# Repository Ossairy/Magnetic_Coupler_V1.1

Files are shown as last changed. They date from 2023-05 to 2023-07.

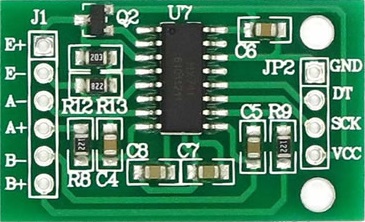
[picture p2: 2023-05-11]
PCB Design/vertion 4/3d/hx711.jpeg

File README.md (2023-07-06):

# Magnetic_Coupler

Project Objective :  
   
    the project objective is to design and manufacture Motor testing setup.
    
Project Duration :
    
    August 2021 ; during my internship period in MRS research Lab -Multi Robot Systems- in german university in cairo.
    
Project Description :   
    First the system is designed and modeled on Solidworks and then the designed parts is manufactured using Laser cutting machine , conventional Lathe , conventional milling machine ,and CNC bending machine. It was desired to measure the torque of a motor that wanted to be tested however applying so much force on the motor shaft may hurt the motor ,so I choosed the magnetic coupler to be added to the system to add the following :
        - Mechanical fusing.
        - No load starting.
At the end the system succeded to acheive the desired objective to measure the motor torque , no load speed electrical power ,and efficiency.

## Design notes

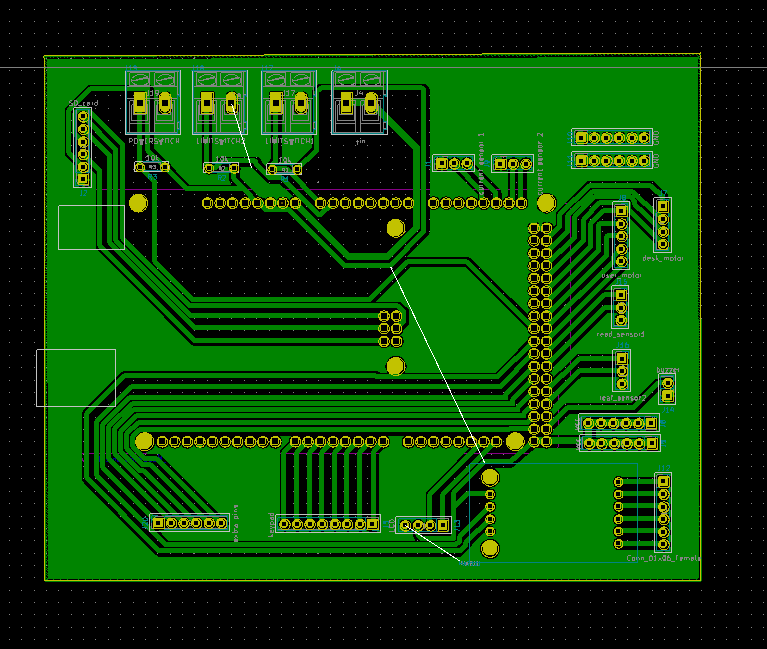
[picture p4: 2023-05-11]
PCB Design/vertion 4/pcb.PNG

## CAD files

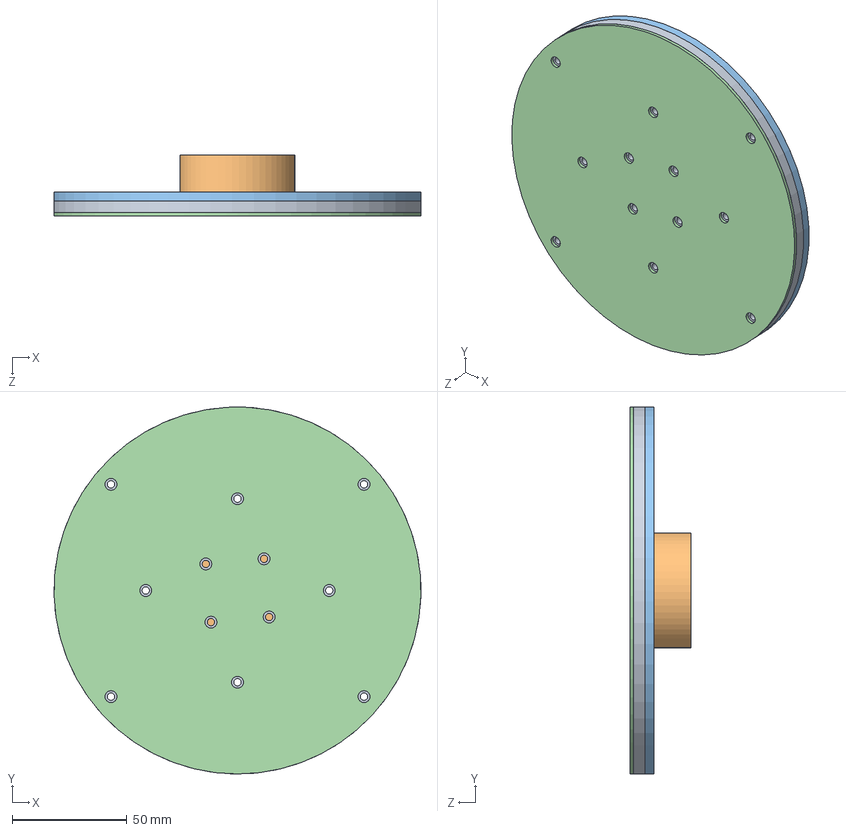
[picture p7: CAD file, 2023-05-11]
3D_Modeling/Magnitic gear assem/Magnitic gear Assem.SLDASM
160.0 x 160.0 x 26.5 mm
Magnitic Disk
Disk holder
Magnet Back limit
magnetic gear cover
Magnet x 18

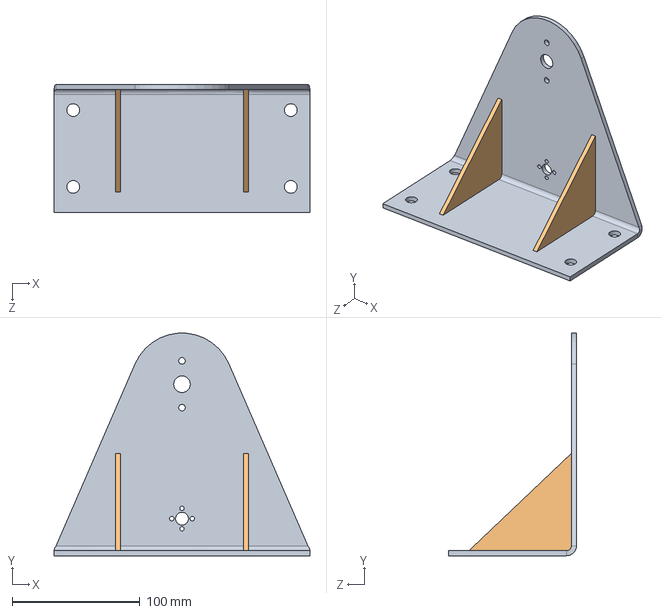
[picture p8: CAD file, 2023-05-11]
3D_Modeling/Sheet Metal/Driven Holder Assem.SLDASM
200.0 x 173.8 x 100.0 mm
Sheet Metal driven holder
Driven holder rip x 2

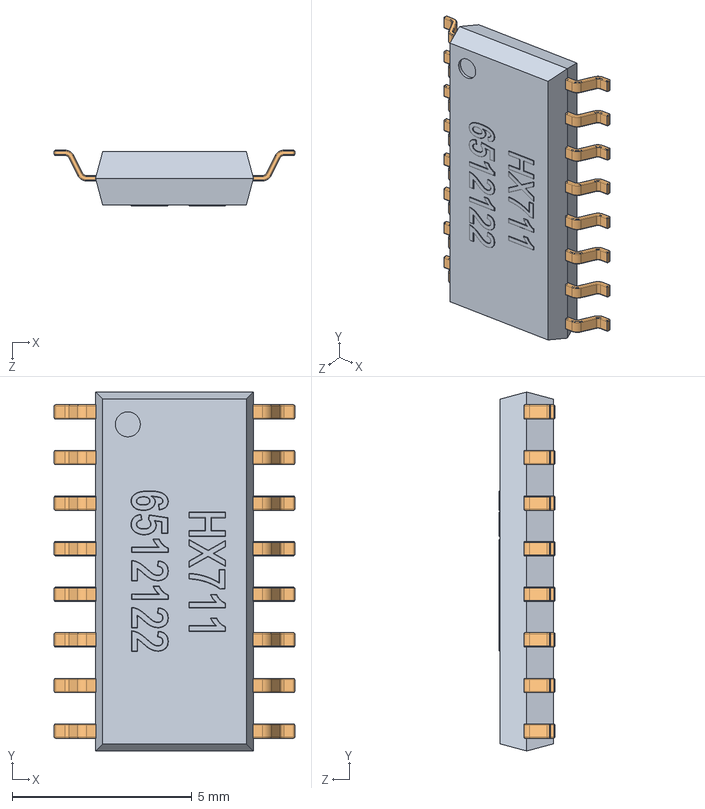
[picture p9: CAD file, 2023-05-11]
PCB Design/vertion 4/3d/HX711_SOP16.SLDASM
6.70 x 10.0 x 1.56 mm
base_HX711
pino_HX711 x 16

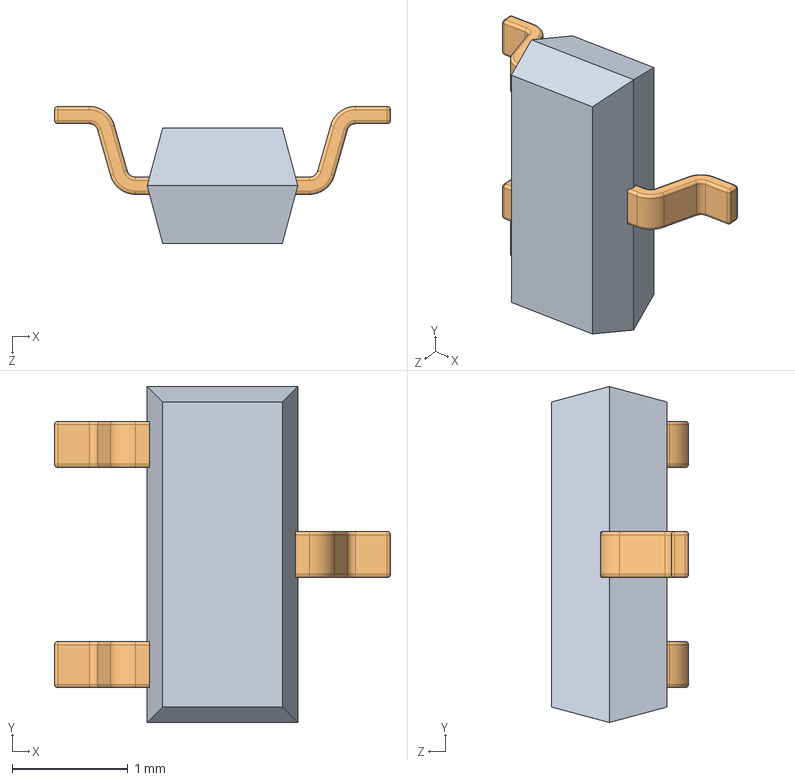
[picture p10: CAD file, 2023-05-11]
PCB Design/vertion 4/3d/SOT23.SLDASM
2.90 x 2.90 x 1.19 mm
TRANSISTOR_SOT23
PINO_SOT23 x 3

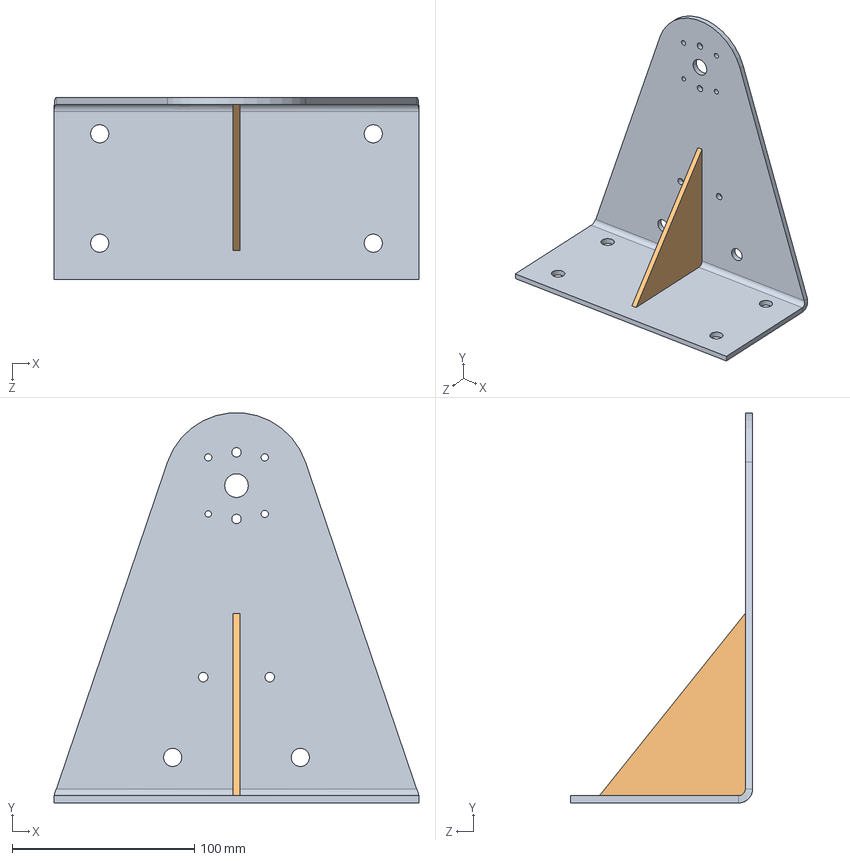
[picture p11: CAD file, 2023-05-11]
3D_Modeling/Sheet Metal/Driver Holder Assem.SLDASM
200.0 x 213.8 x 100.0 mm
Sheet Metal driver holder
Driver holder rib

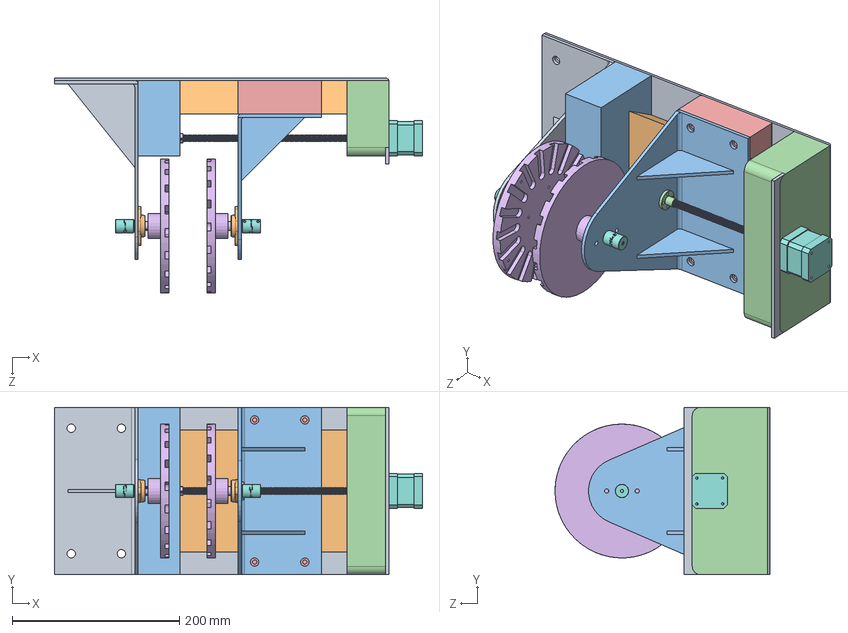
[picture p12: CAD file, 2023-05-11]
3D_Modeling/Assem1.SLDASM
440.0 x 200.0 x 257.0 mm
chassis
lower linear traveller
screw supporter
Motor holder
Upper linear traveller x 2
608RS x 3
MOSCAM2,5 x 2
Nema 17
driver holder
KFL08 x 2
driven holder
8mm Lead Screw
screw bar
magnitic gear x 2
bar x 2
coupling_5x8 x 2

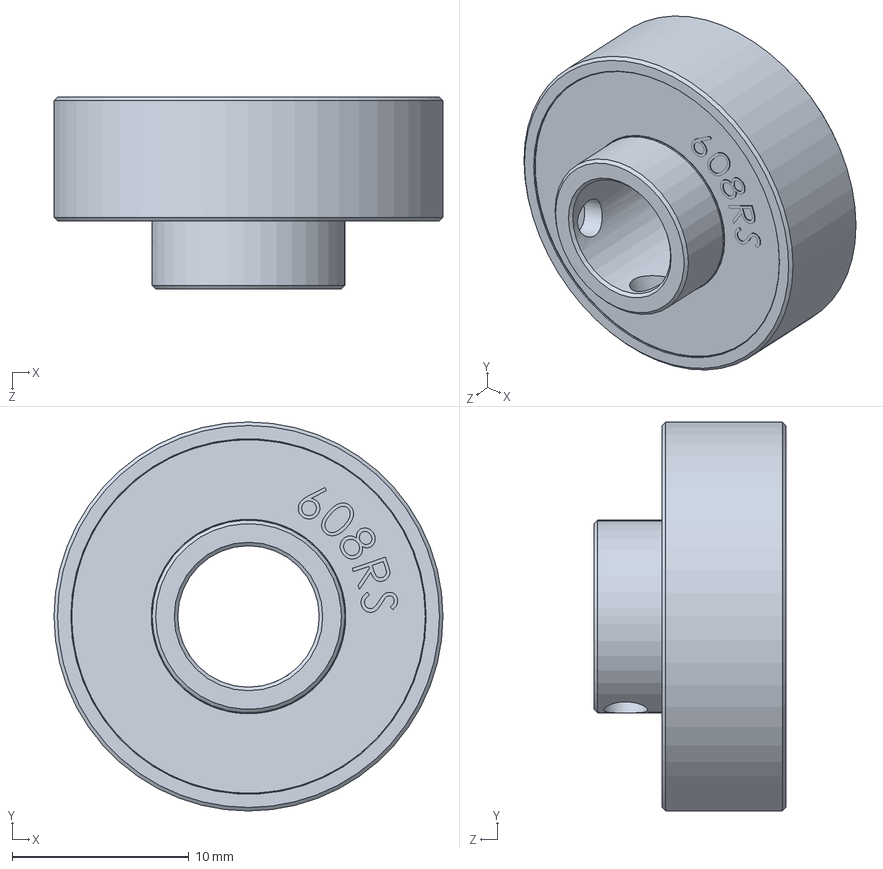
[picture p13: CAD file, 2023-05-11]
3D_Modeling/608RS.SLDPRT
22.0 x 22.0 x 10.9 mm

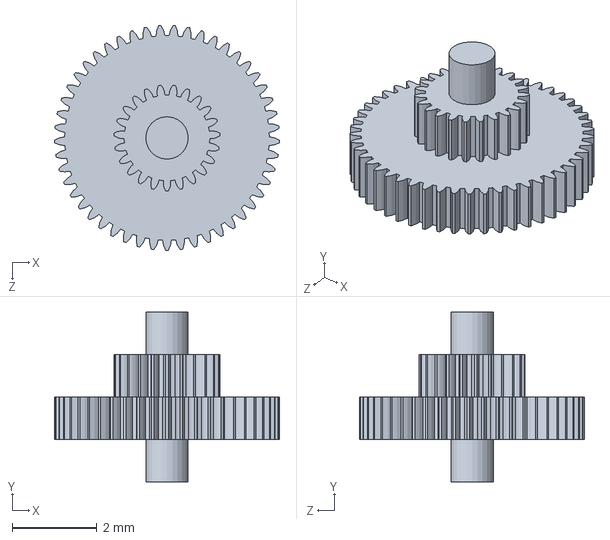
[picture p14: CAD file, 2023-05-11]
3D_Modeling/Motor 12V/Motor JGB37-545/Part 4.SLDPRT
5.30 x 4.00 x 5.30 mm

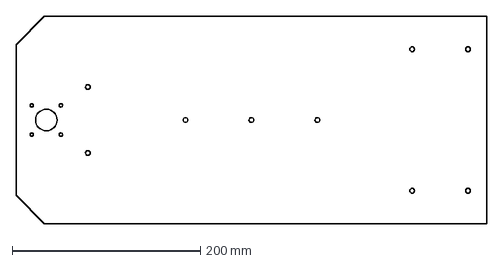
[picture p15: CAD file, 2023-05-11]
3D_Modeling/Sheet Metal/dxf files/Flat pattern - Sheet Metal chassis.DXF
499.8 x 220.0 mm

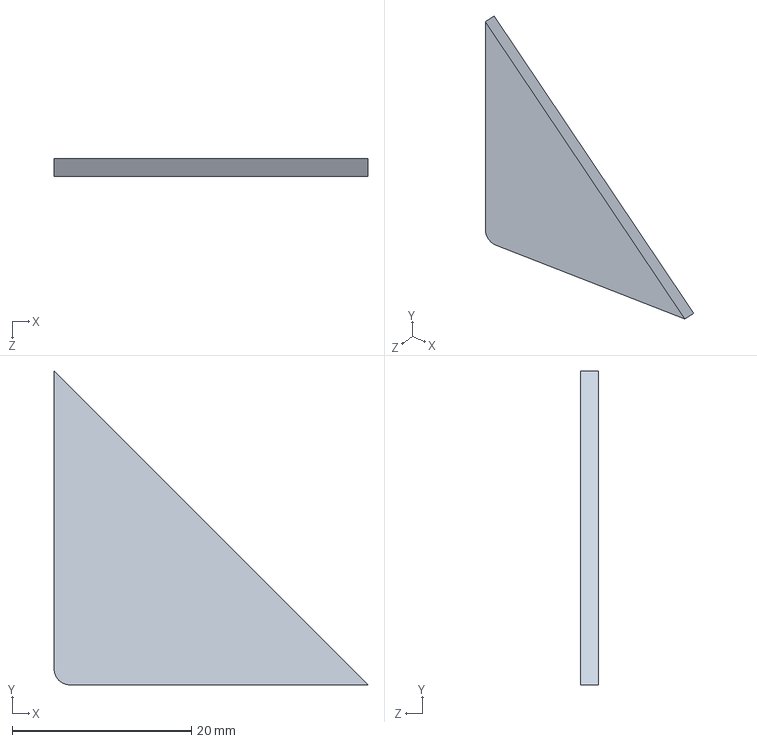
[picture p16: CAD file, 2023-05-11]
3D_Modeling/Sheet Metal/Nema17 rib.SLDPRT
35.0 x 35.0 x 2.00 mm

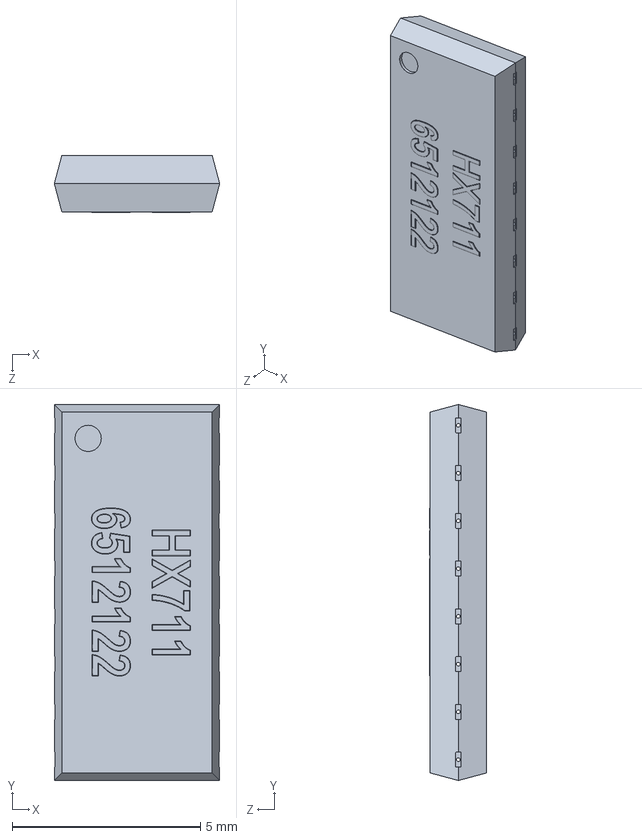
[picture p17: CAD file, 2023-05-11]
PCB Design/vertion 4/3d/base_HX711.SLDPRT
4.40 x 10.0 x 1.52 mm

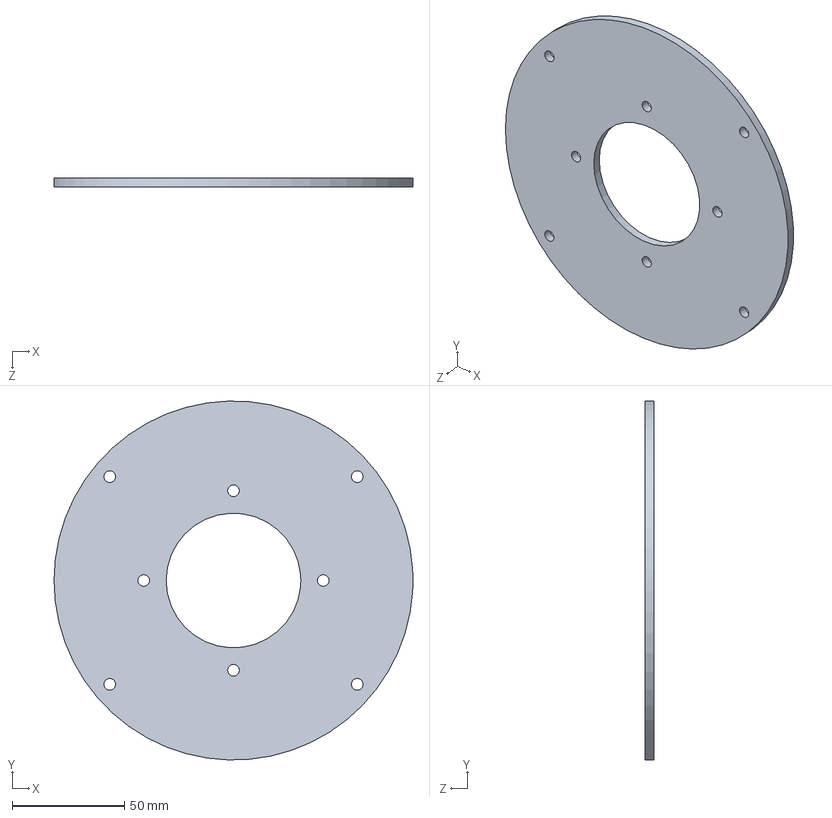
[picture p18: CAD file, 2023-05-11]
3D_Modeling/Magnitic gear assem/Magnet Back limit.SLDPRT
160.0 x 159.9 x 4.00 mm

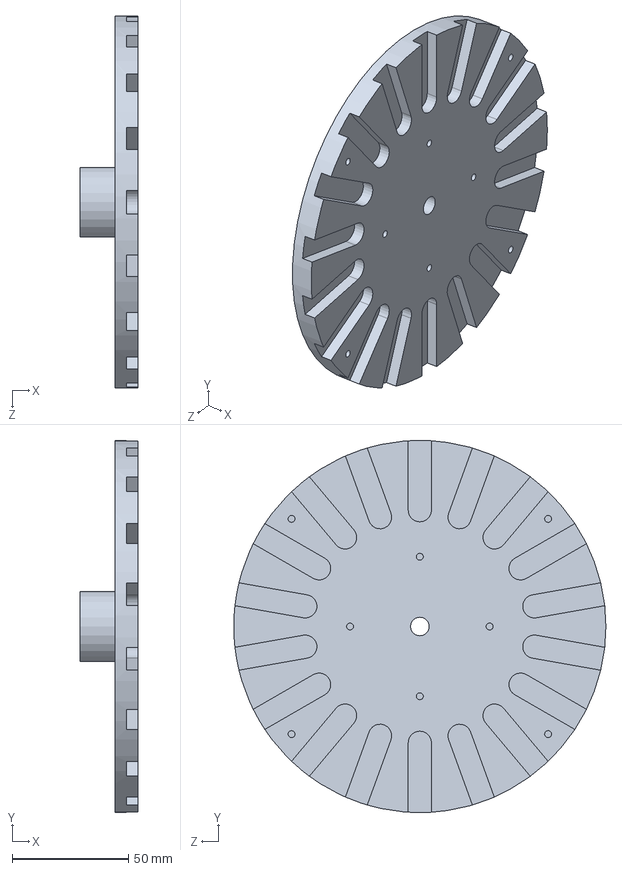
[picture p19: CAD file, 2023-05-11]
3D_Modeling/magnitic gear.SLDPRT
25.0 x 159.9 x 159.9 mm

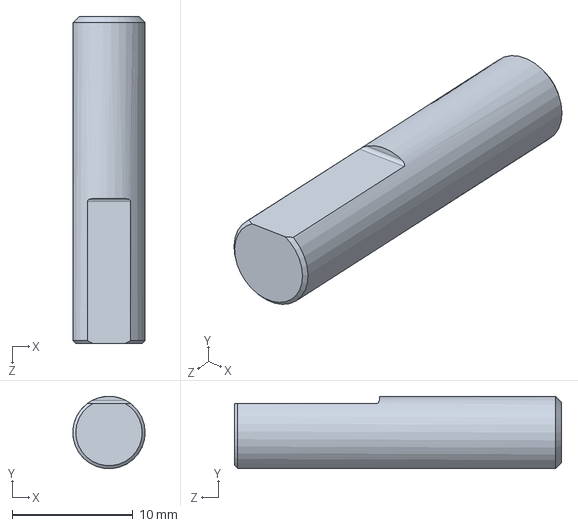
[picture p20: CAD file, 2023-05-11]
3D_Modeling/Motor 12V/Motor JGB37-545/Shaft.SLDPRT
6.00 x 5.99 x 27.1 mm

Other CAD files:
3D_Modeling/Sheet Metal/dxf files/Flat pattern - Sheet Metal Nema17 LBracket.DXF
PCB Design/vertion 4/3d/ArduinoMega.SLDPRT
3D_Modeling/Magnitic gear assem/Disk holder.SLDPRT
3D_Modeling/Motor 12V/Motor JGB37-545/Motor body.SLDPRT
3D_Modeling/Drawing/Modified magnitic gear drawing.SLDDRW
3D_Modeling/Drawing/Nema17 LBracket drawing.SLDDRW
3D_Modeling/Drawing/Upper linear traveller drawing.SLDDRW
3D_Modeling/Drawing/chassis Drawing.SLDDRW
3D_Modeling/Drawing/driven holder drawing.SLDDRW
3D_Modeling/Drawing/driver holder drawing.SLDDRW
3D_Modeling/Drawing/lower linear traveller drawing.SLDDRW
3D_Modeling/Drawing/magnitic gear drawing.SLDDRW
3D_Modeling/KFL08.SLDPRT
3D_Modeling/Lead Screw.SLDPRT
3D_Modeling/Load_cell_sensor-5_kg v1.step.SLDPRT
3D_Modeling/M3 Bolt.SLDPRT
3D_Modeling/M3 nut.SLDPRT
3D_Modeling/M5 bolt.SLDPRT
3D_Modeling/M5 nut.SLDPRT
3D_Modeling/Magnet.SLDPRT
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

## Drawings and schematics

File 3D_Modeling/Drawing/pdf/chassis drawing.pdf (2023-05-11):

6

5

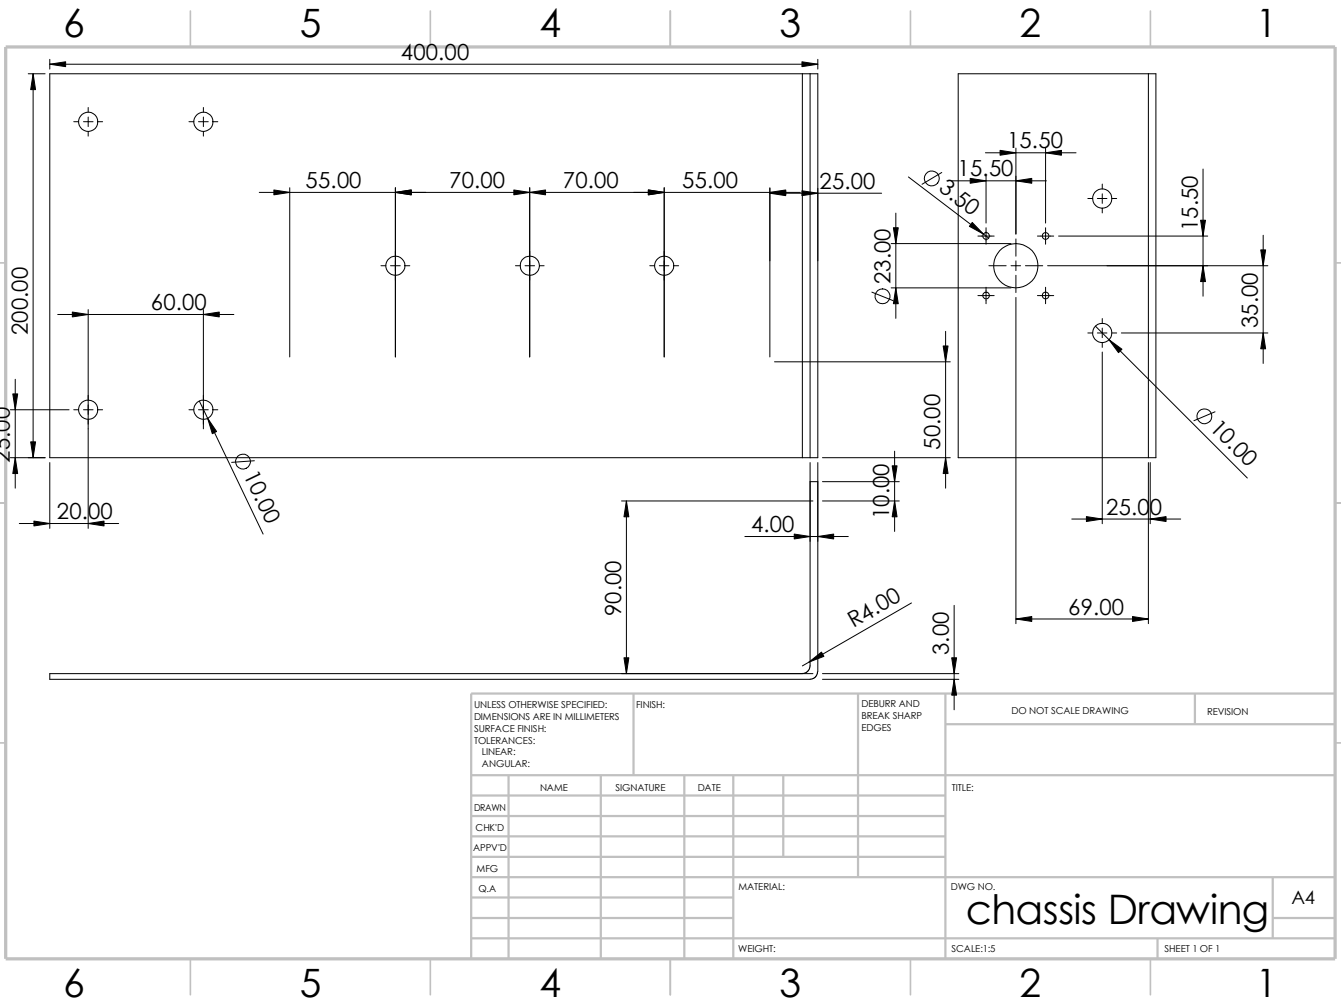
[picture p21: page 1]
WEIGHT:; SCALE:1:5; SHEET 1 OF 1; REVISION; FINISH:; EDGES; DEBURR AND BREAK SHARP; chassis Drawing ²³.00

DO NOT SCALE DRAWING UNLESS OTHERWISE SPECIFIED:
DIMENSIONS ARE IN MILLIMETERS
SURFACE FINISH:
TOLERANCES:
LINEAR:
ANGULAR:

NAME | SIGNATURE | DATE | | | | TITLE:

DRAWN
CHK'D
APPV'D
Q.A | | | | MATERIAL: | DWG NO. | A4

MFG

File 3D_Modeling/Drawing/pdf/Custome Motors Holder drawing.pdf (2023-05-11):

6

5

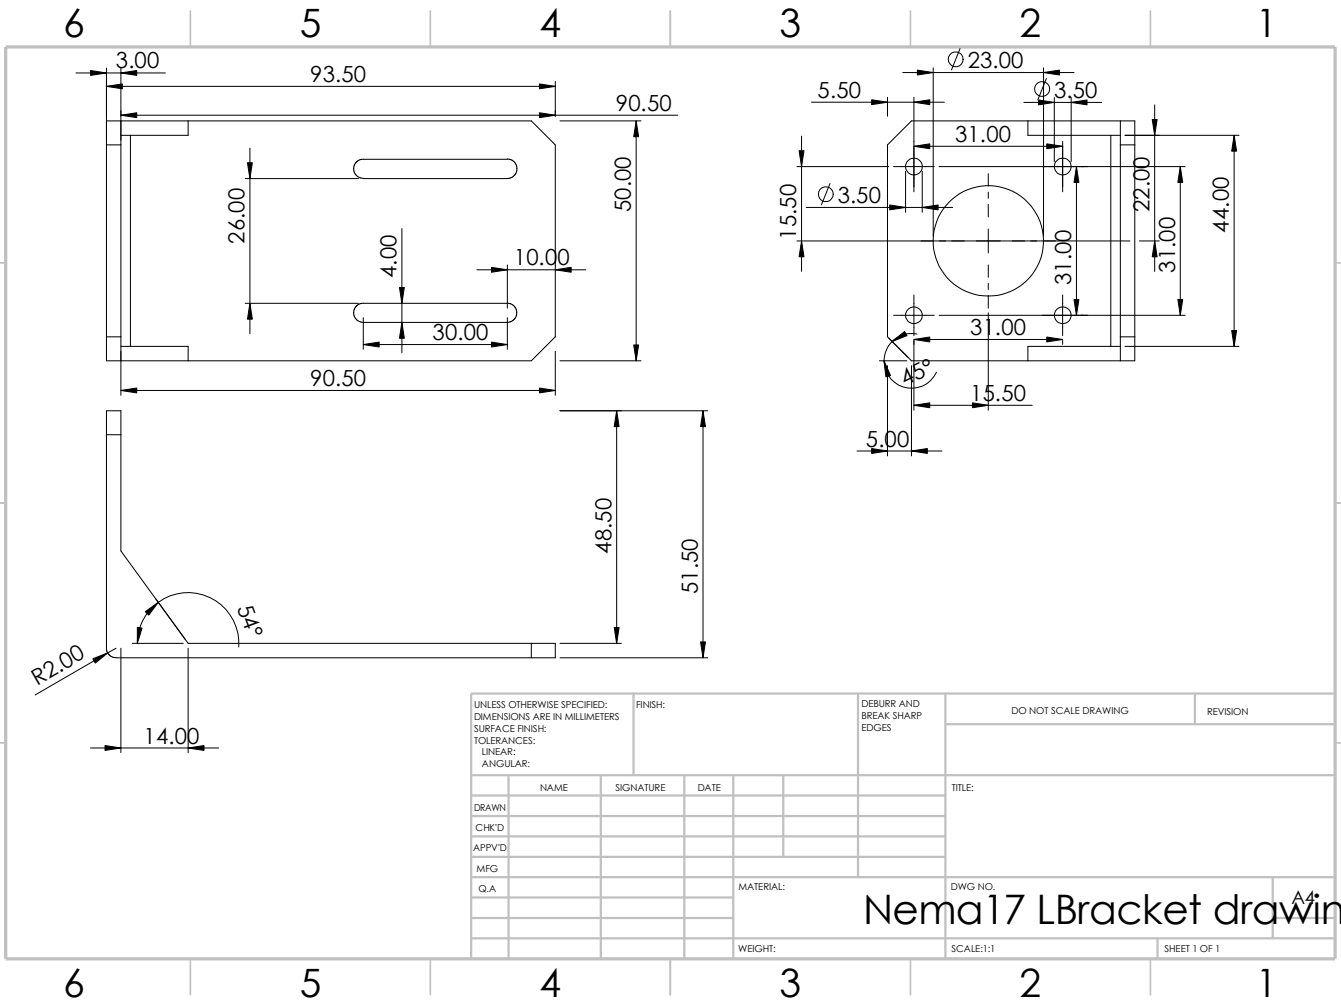
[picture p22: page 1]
WEIGHT:; SCALE:1:1; SHEET 1 OF 1; REVISION; FINISH:; EDGES; DEBURR AND BREAK SHARP; Nema17 LBracket drawing ⁴⁸.50

DO NOT SCALE DRAWING UNLESS OTHERWISE SPECIFIED:
DIMENSIONS ARE IN MILLIMETERS
SURFACE FINISH:
TOLERANCES:
LINEAR:
ANGULAR:

NAME | SIGNATURE | DATE | | | | TITLE:

DRAWN
CHK'D
APPV'D
Q.A | | | | MATERIAL: | DWG NO. | A4

MFG

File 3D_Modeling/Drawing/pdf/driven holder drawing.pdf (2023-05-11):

6

5

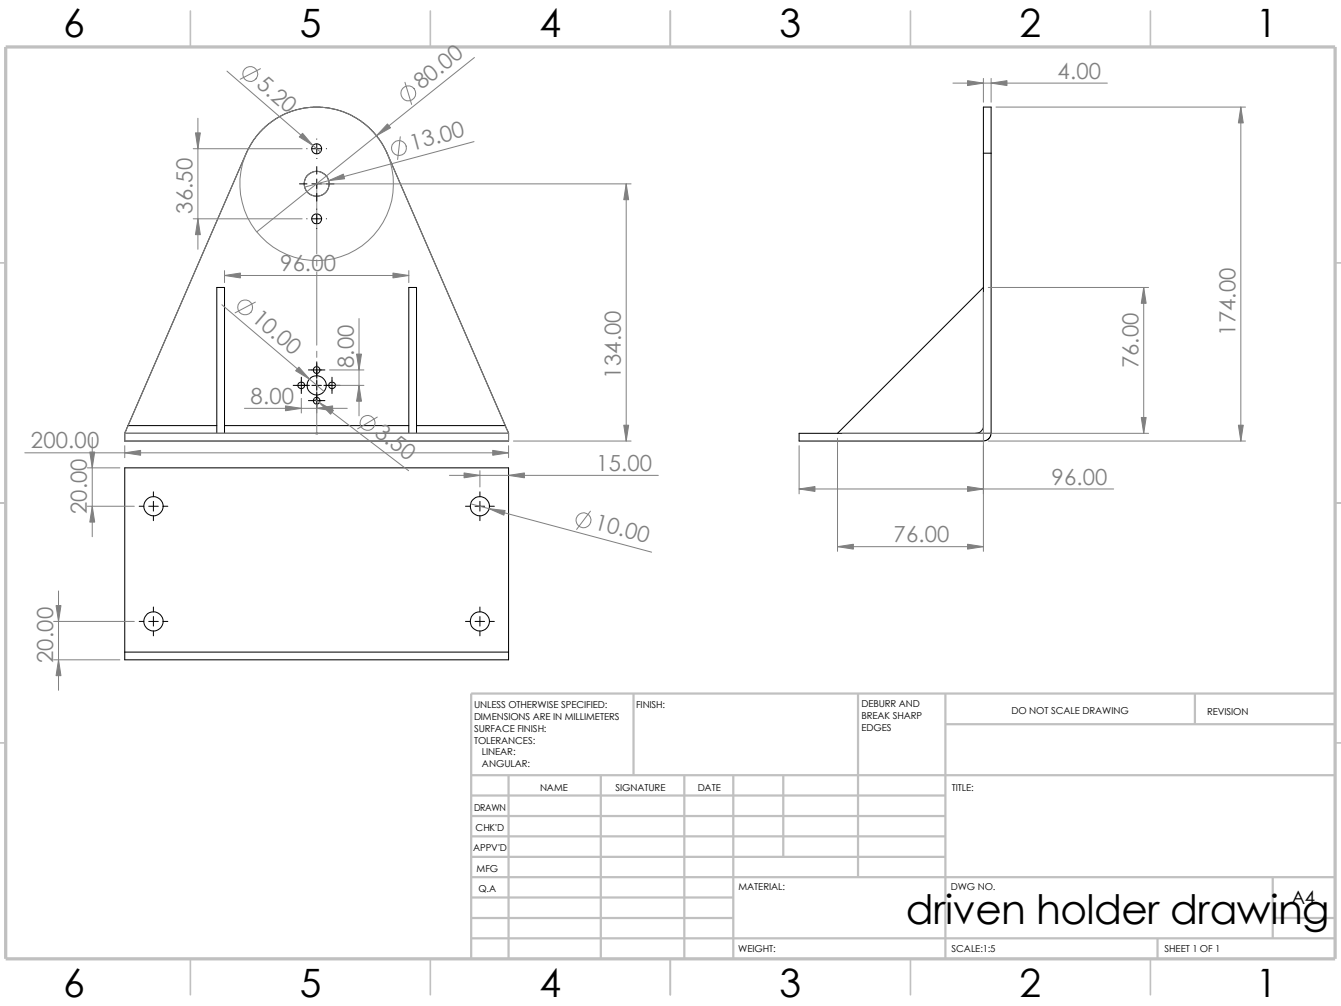
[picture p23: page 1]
WEIGHT:; SCALE:1:5; SHEET 1 OF 1; REVISION; FINISH:; EDGES; DEBURR AND BREAK SHARP

DO NOT SCALE DRAWING UNLESS OTHERWISE SPECIFIED:
DIMENSIONS ARE IN MILLIMETERS
SURFACE FINISH:
TOLERANCES:
LINEAR:
ANGULAR:

NAME | SIGNATURE | DATE | | | | TITLE:

DRAWN
CHK'D
APPV'D
Q.A | | | | MATERIAL: driven holder drawing | DWG NO. | A4

MFG

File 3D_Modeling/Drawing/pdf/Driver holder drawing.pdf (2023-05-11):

6

5

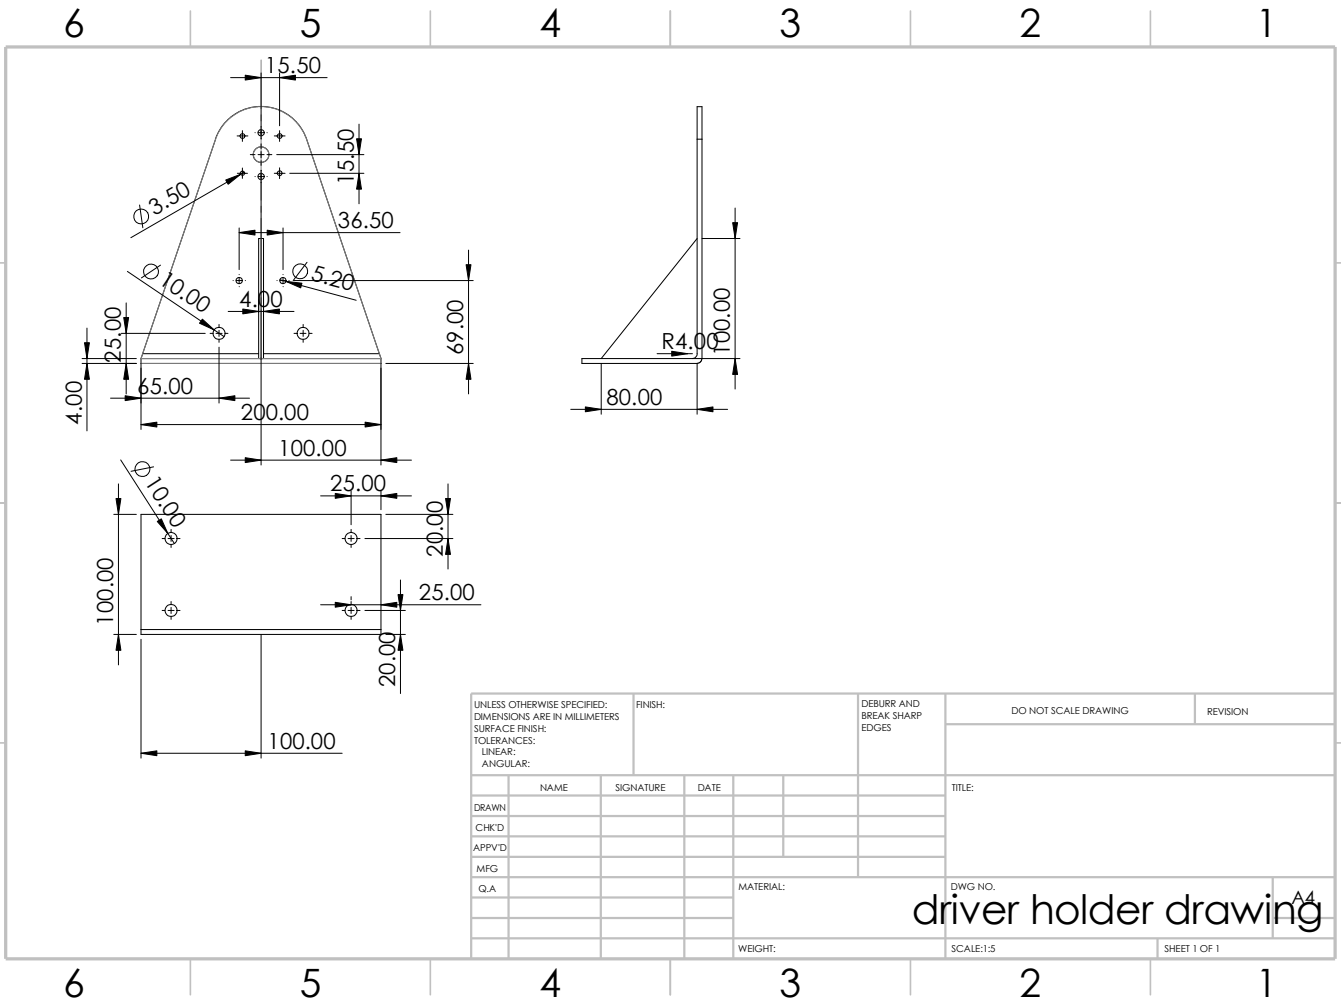
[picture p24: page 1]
WEIGHT:; SCALE:1:5; SHEET 1 OF 1; REVISION; FINISH:; EDGES; DEBURR AND BREAK SHARP; 100.00 ¹⁰⁰.00

DO NOT SCALE DRAWING UNLESS OTHERWISE SPECIFIED:
DIMENSIONS ARE IN MILLIMETERS
SURFACE FINISH:
TOLERANCES:
LINEAR:
ANGULAR:

NAME | SIGNATURE | DATE | | | | TITLE:

DRAWN
CHK'D
APPV'D
Q.A | | | | MATERIAL: driver holder drawing | DWG NO. | A4

MFG

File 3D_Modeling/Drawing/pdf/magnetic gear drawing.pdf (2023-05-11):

6

5

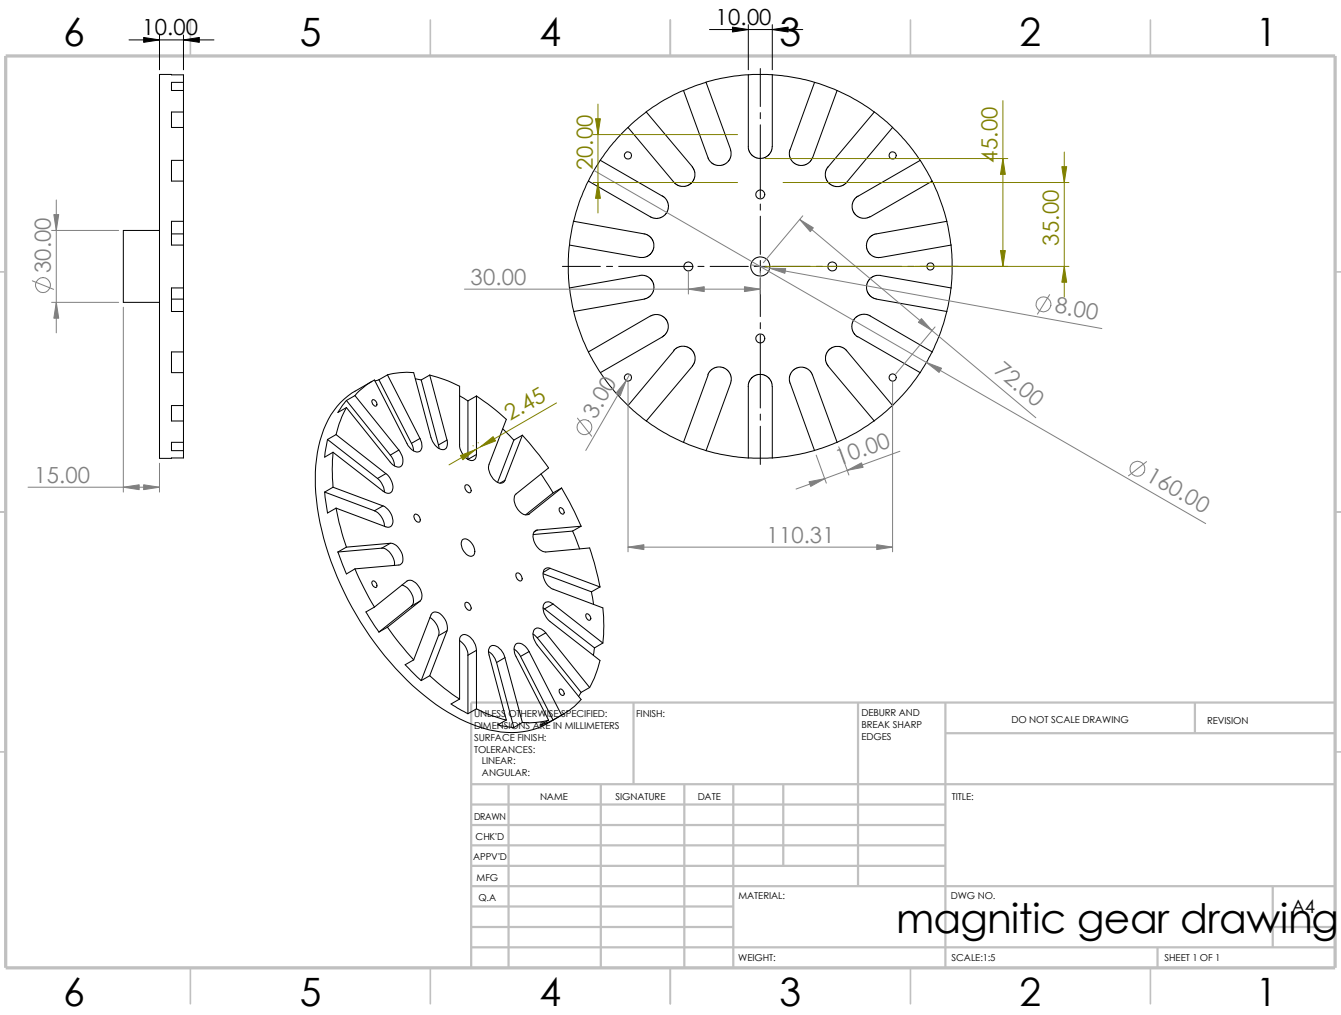
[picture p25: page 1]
WEIGHT:; SCALE:1:5; SHEET 1 OF 1; FINISH:; EDGES; DO NOT SCALE DRAWING; REVISION; DEBURR AND BREAK SHARP

UNLESS OTHERWISE SPECIFIED:
DIMENSIONS ARE IN MILLIMETERS
SURFACE FINISH:
TOLERANCES:
LINEAR:
ANGULAR:

NAME | SIGNATURE | DATE | | | | TITLE:

DRAWN
CHK'D
APPV'D

MFG
Q.A | | | | MATERIAL: magnitic gear drawing | DWG NO. | A4

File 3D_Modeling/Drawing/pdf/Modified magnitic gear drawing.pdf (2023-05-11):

6

5

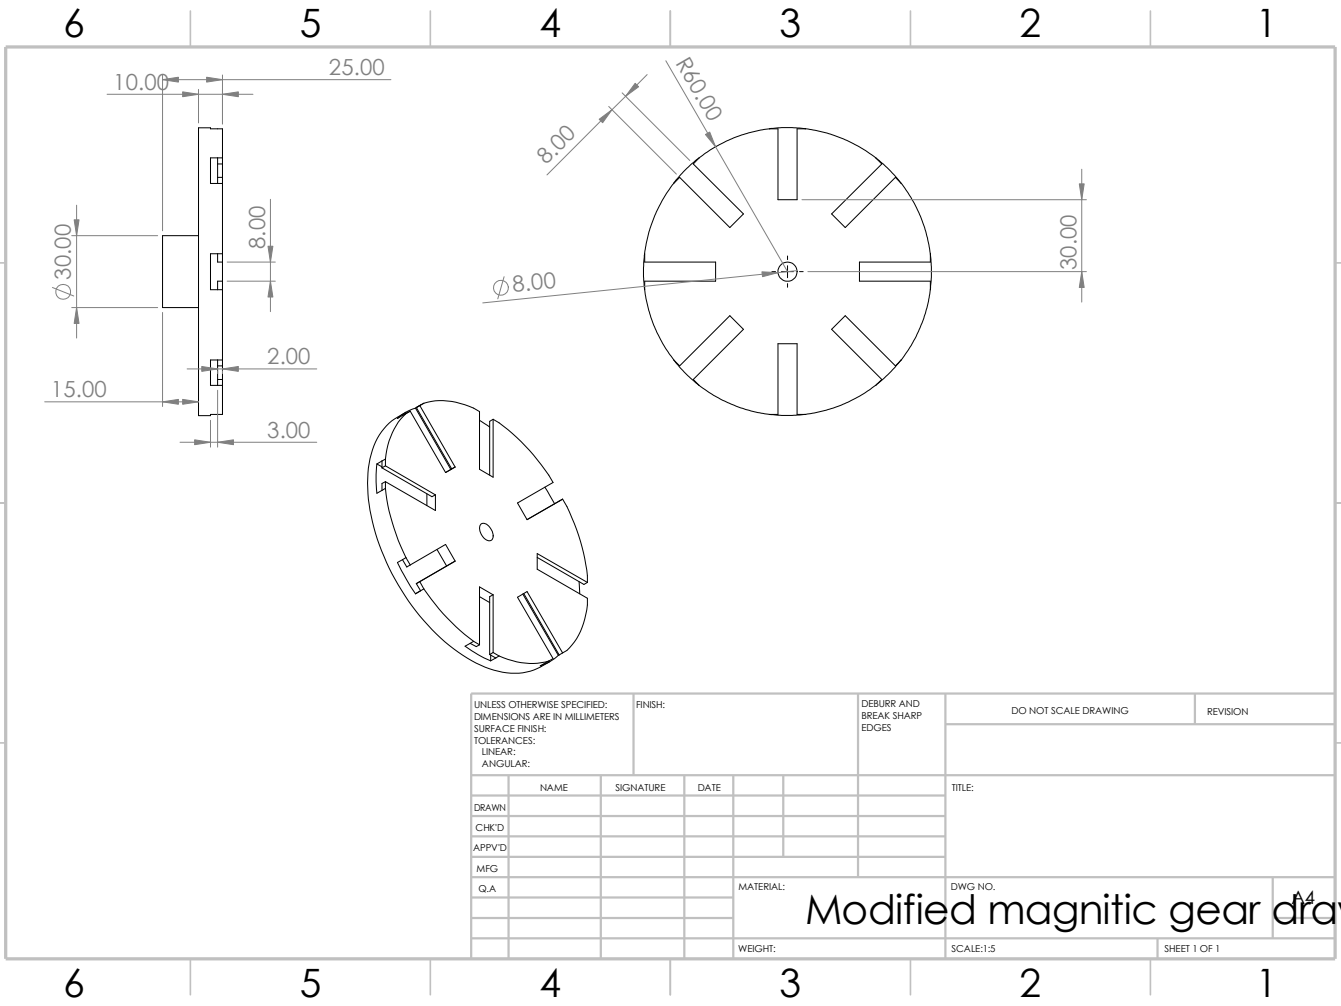
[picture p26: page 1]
WEIGHT:; SHEET 1 OF 1; SCALE:1:5; FINISH:; EDGES; DO NOT SCALE DRAWING; REVISION; DEBURR AND BREAK SHARP

UNLESS OTHERWISE SPECIFIED:
DIMENSIONS ARE IN MILLIMETERS
SURFACE FINISH:
TOLERANCES:
LINEAR:
ANGULAR:

NAME | SIGNATURE | DATE | | | | TITLE:

DRAWN
CHK'D
APPV'D

MFG
Q.A | | | | MATERIAL: | DWG NO. | A4

Modified magnitic gear drawing

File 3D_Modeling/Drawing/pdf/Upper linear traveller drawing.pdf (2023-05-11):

6

5

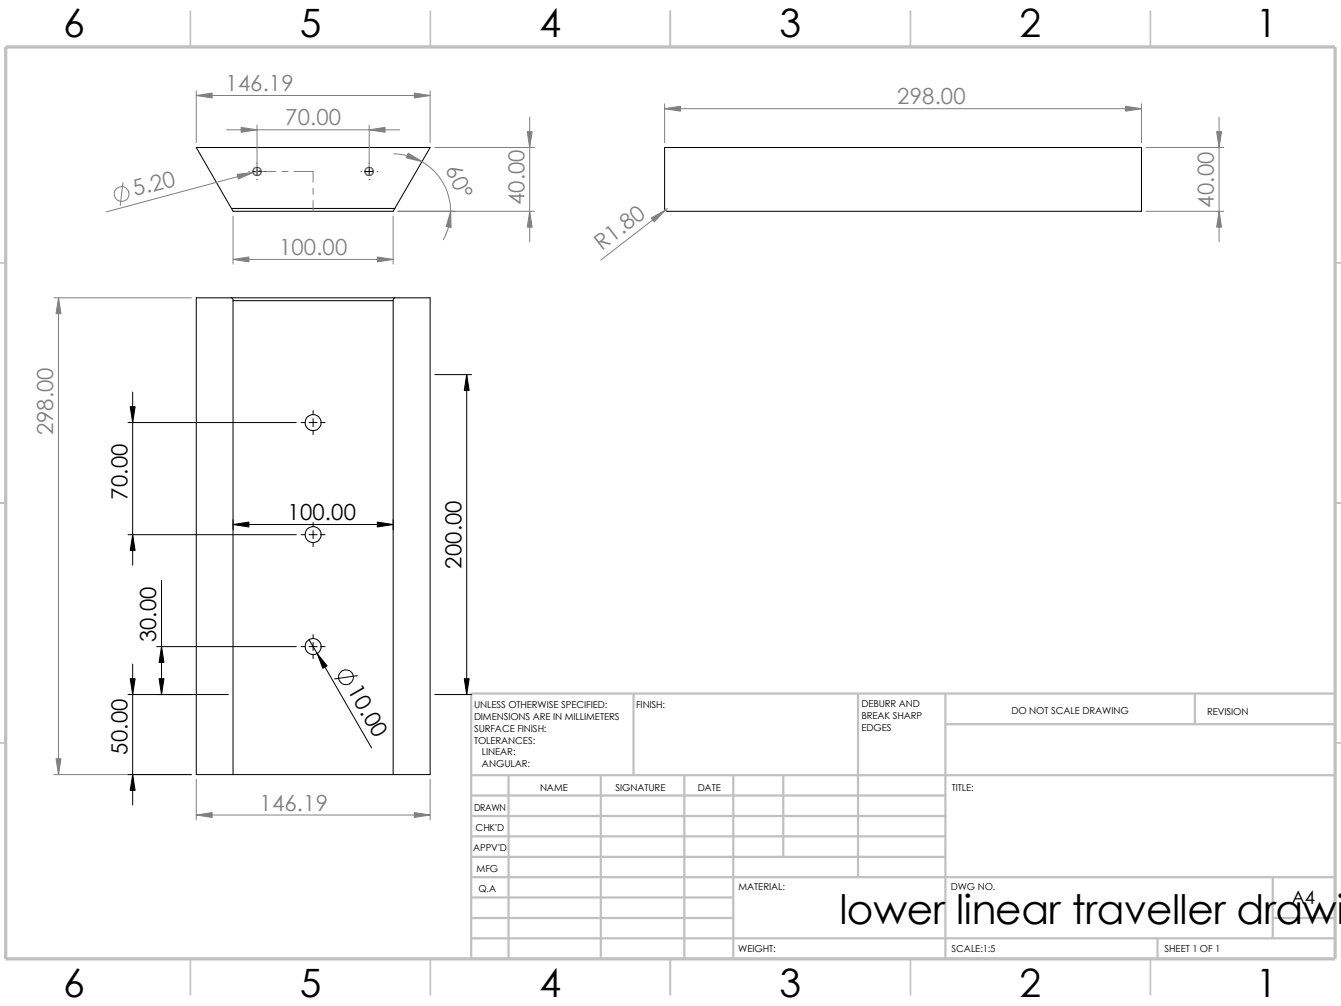
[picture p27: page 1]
WEIGHT:; SCALE:1:5; SHEET 1 OF 1; FINISH:; EDGES; DO NOT SCALE DRAWING; REVISION; DEBURR AND BREAK SHARP; 146.19 ²⁹⁸.00

UNLESS OTHERWISE SPECIFIED:
DIMENSIONS ARE IN MILLIMETERS
SURFACE FINISH:
TOLERANCES:
LINEAR:
ANGULAR:

NAME | SIGNATURE | DATE | | | | TITLE:

DRAWN
CHK'D
APPV'D

MFG
Q.A | | | | MATERIAL: | DWG NO. | A4

lower linear traveller drawing

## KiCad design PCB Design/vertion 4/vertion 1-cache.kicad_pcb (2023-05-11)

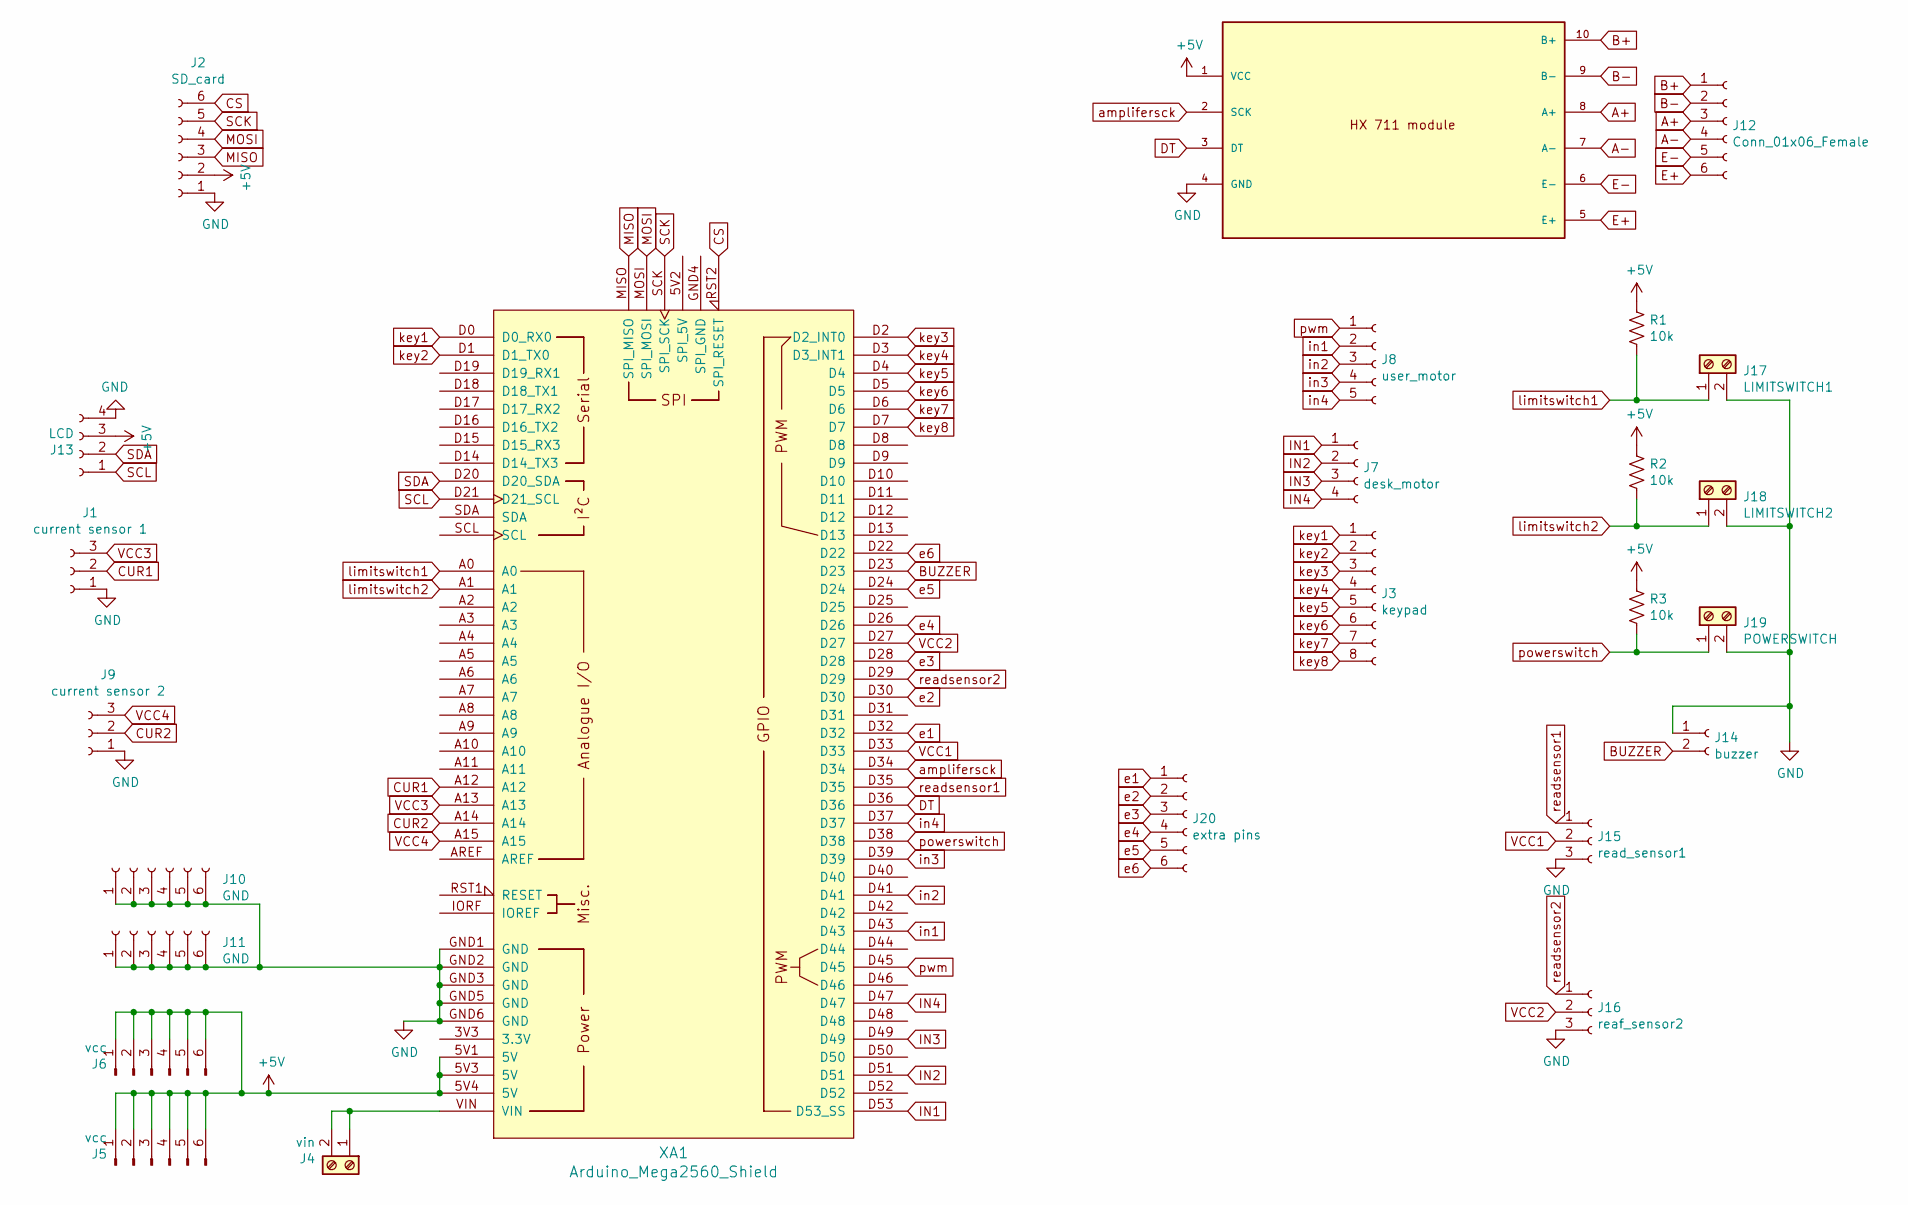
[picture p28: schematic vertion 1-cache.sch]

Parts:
HX7111: HX711
J1: current sensor 1; PinSocket_1x03_P2.54mm_Vertical
J2: SD_card; PinSocket_1x06_P2.54mm_Vertical
J3: keypad; PinSocket_1x08_P2.54mm_Vertical
J4: vin; TerminalBlock_Altech_AK300-2_P5.00mm
J5, J6: vcc; PinHeader_1x06_P2.54mm_Vertical
J7: desk_motor; PinSocket_1x04_P2.54mm_Vertical
J8: user_motor; PinSocket_1x05_P2.54mm_Vertical
J9: current sensor 2; PinSocket_1x03_P2.54mm_Vertical
J10, J11: GND; PinHeader_1x06_P2.54mm_Vertical
J12: Conn_01x06_Female; PinSocket_1x06_P2.54mm_Vertical
J13: LCD; PinSocket_1x04_P2.54mm_Vertical
J14: buzzer; PinSocket_1x02_P2.54mm_Vertical
J15: read_sensor1; PinSocket_1x03_P2.54mm_Vertical
J16: reaf_sensor2; PinSocket_1x03_P2.54mm_Vertical
J17: LIMITSWITCH1; TerminalBlock_Altech_AK300-2_P5.00mm
J18: LIMITSWITCH2; TerminalBlock_Altech_AK300-2_P5.00mm
J19: POWERSWITCH; TerminalBlock_Altech_AK300-2_P5.00mm
J20: extra pins; PinSocket_1x06_P2.54mm_Vertical
R1, R2, R3: 10k; R_Axial_DIN0204_L3.6mm_D1.6mm_P5.08mm_Horizontal
XA1: Arduino_Mega2560_Shield

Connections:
+5V: HX7111.1 (VCC), J2.2, J5.1, J5.2, J5.3, J5.4, J5.5, J5.6, J6.1, J6.2, J6.3, J6.4, J6.5, J6.6, J13.3, R1.1, R2.1, R3.1, XA1.5V1 (5V), XA1.5V3 (5V), XA1.5V4 (5V)
A+: HX7111.8 (A+), J12.3
A-: HX7111.7 (A-), J12.4
B+: HX7111.10 (B+), J12.1
B-: HX7111.9 (B-), J12.2
BUZZER: J14.2, XA1.D23
CS: J2.6, XA1.RST2 (SPI_RESET)
CUR1: J1.2, XA1.A12
CUR2: J9.2, XA1.A14
DT: HX7111.3 (DT), XA1.D36
E+: HX7111.5 (E+), J12.6
E-: HX7111.6 (E-), J12.5
GND: HX7111.4 (GND), J1.1, J2.1, J9.1, J10.1, J10.2, J10.3, J10.4, J10.5, J10.6, J11.1, J11.2, J11.3, J11.4, J11.5, J11.6, J13.4, J14.1, J15.3, J16.3, J17.2, J18.2, J19.2, XA1.GND1 (GND), XA1.GND2 (GND), XA1.GND3 (GND), XA1.GND5 (GND), XA1.GND6 (GND)
IN1: J7.1, XA1.D53 (D53_SS)
IN2: J7.2, XA1.D51
IN3: J7.3, XA1.D49
IN4: J7.4, XA1.D47
MISO: J2.3, XA1.MISO (SPI_MISO)
MOSI: J2.4, XA1.MOSI (SPI_MOSI)
unnamed: J4.1, J4.2, XA1.VIN
SCK: J2.5, XA1.SCK (SPI_SCK)
SCL: J13.1, XA1.D21 (D21_SCL)
SDA: J13.2, XA1.D20 (D20_SDA)
VCC1: J15.2, XA1.D33
VCC2: J16.2, XA1.D27
VCC3: J1.3, XA1.A13
VCC4: J9.3, XA1.A15
amplifersck: HX7111.2 (SCK), XA1.D34
e1: J20.1, XA1.D32
e2: J20.2, XA1.D30
e3: J20.3, XA1.D28
e4: J20.4, XA1.D26
e5: J20.5, XA1.D24
e6: J20.6, XA1.D22
in1: J8.2, XA1.D43
in2: J8.3, XA1.D41
in3: J8.4, XA1.D39
in4: J8.5, XA1.D37
key1: J3.1, XA1.D0 (D0_RX0)
key2: J3.2, XA1.D1 (D1_TX0)
key3: J3.3, XA1.D2 (D2_INT0)
key4: J3.4, XA1.D3 (D3_INT1)
key5: J3.5, XA1.D4
key6: J3.6, XA1.D5
key7: J3.7, XA1.D6
key8: J3.8, XA1.D7
limitswitch1: J17.1, R1.2, XA1.A0
limitswitch2: J18.1, R2.2, XA1.A1
powerswitch: J19.1, R3.2, XA1.D38
pwm: J8.1, XA1.D45
readsensor1: J15.1, XA1.D35
readsensor2: J16.1, XA1.D29

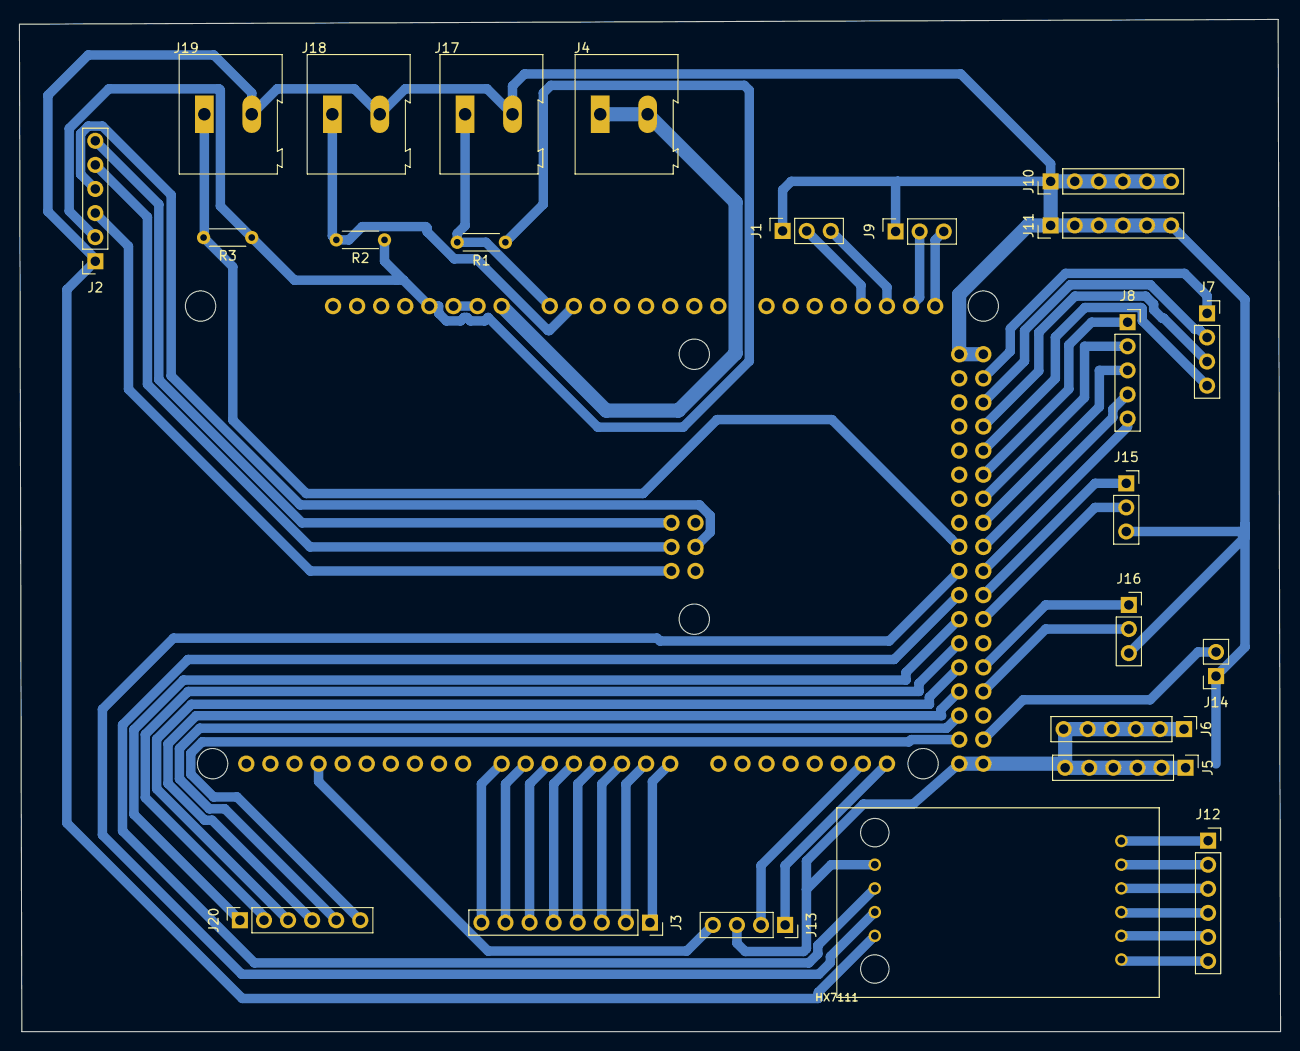
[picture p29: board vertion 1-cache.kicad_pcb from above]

Board: 2 copper layers, 133.0 x 106.8 mm, 25 parts (1 on the bottom side), 52 nets.

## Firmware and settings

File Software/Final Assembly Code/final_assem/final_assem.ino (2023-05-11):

#include <Keypad.h>
#include <Wire.h>
#include <Adafruit_GFX.h>
#include <Adafruit_SSD1306.h>

#include <Stepper.h>

#include "HX711.h"

#define calibration_factor -17090.00 //This value is obtained using the SparkFun_HX711_Calibration sketch

#define LOADCELL_DOUT_PIN  36
#define LOADCELL_SCK_PIN  34

HX711 scale;

int torque;
const int stepsPerRevolution = 200;
Stepper myStepper = Stepper(stepsPerRevolution, 53, 51, 49, 47);

float power;
float current ;

int a =  0;
float value =0;
int avgRpm ;
int count=0;

float loops;
int rpm = 0;
int b [30] ;
float maxSpeed =0;
float minSpeed=0;
float accelerasion;



//int a =  0;
//float value =0;
int a2 =  0;
float value2 =0;
//unsigned long long t =0;
//loat loops;
float loops2;
//int rpm = 0;
int rpm2 = 0;
//float maxSpeed =0;
//float accelerasion;
int maxtorque;

// Declaration for an SSD1306 display connected to I2C (SDA, SCL pins)
//Adafruit_SSD1306 display(SCREEN_WIDTH, SCREEN_HEIGHT, &Wire, -1);

const byte ROWS = 4;
const byte COLS = 4;

char hexaKeys[ROWS][COLS] = {
  {'1', '2', '3', '+'},
  {'4', '5', '6', '-'},
  {'7', '8', '9', 'x'},
  {'.', '0', '=', '/'}
};
 
// Connections to Arduino
byte rowPins[ROWS] = {7, 6, 5, 4}; //connect to the row pinouts of the keypad
byte colPins[COLS] = {3, 2, 44, 22}; //connect to the column pinouts of the keypad
 
// Create keypad object
Keypad customKeypad = Keypad(makeKeymap(hexaKeys), rowPins, colPins, ROWS, COLS);
 /*
class Motor {
  public :
   String Name ;
   int Torque ; 
   int Maxrpm ; 
   int Power ; 
   int efficiency ;
   public:
    Motor (String Name , int Torque , int Maxrpm , int Power , int efficiency ){
      this->Name = Name;
      this->Torque = Torque;
      this->Maxrpm = Maxrpm;
      this->Power = Power;
      this->efficiency = efficiency;
      
      init();
      
      }
  int measureSPEED (){
  
Serial.println(" qq measuring SPEED (rpm) ......");

}
int measurePOWER (){
  
Serial.println("  qq measuring POWER (rpm) ......");

}
int measureTORQUE (){
  
Serial.println("  qq measuring TORQUE (rpm) ......");

}
  
  };*/

//Motor Nema17 =Motor("Nema17",260,1500,30,80);
//Motor Nema23 =Motor("Nema23",600,1800,40,90);
bool Measureflag = false;
bool Motorflag =false;
bool Modeflag =false;
//Motor  recordedmotors [] = {Nema17 , Nema23};
int arrlength = 2;
void setup() {
//Serial.begin(115200);
pinMode(23,OUTPUT);

pinMode(25 , INPUT) ;

pinMode(43 , OUTPUT) ;
pinMode(45 , OUTPUT) ;
pinMode(24 , INPUT) ;
digitalWrite (13, LOW) ;
pinMode(41 , OUTPUT) ;

pinMode(53,OUTPUT);
pinMode(51,OUTPUT);
pinMode(47,OUTPUT);

pinMode(27 , OUTPUT);
digitalWrite(27,HIGH);
pinMode(33,OUTPUT);
digitalWrite(33,HIGH);
pinMode(A13,OUTPUT);
digitalWrite(A13,HIGH);
pinMode(A15,OUTPUT);
digitalWrite(A15,HIGH);
//pinMode(33,OUTPUT);


Serial.begin(9600);
 scale.begin(LOADCELL_DOUT_PIN, LOADCELL_SCK_PIN);
  scale.set_scale(calibration_factor);
  //scale.tare();
pinMode(31,INPUT);
pinMode(29,INPUT);
}

void loop() {
 
if(!Modeflag)
  getMode();

if(digitalRead(38))
 Modeflag = false;


}


void testandreport(){
Serial.println("DO YOU WANT RECORDED DATA OF STANDARD MOTORS");
Serial.println(" 1) Yes. ");
Serial.println(" 2) Compare with my data. ");
Serial.println(" 3) Back. ");
  while(1){
    char customKey = customKeypad.getKey();
    if(customKey){
       if(customKey == '1'){
        //Motor a = choosefromrecorded();
        //Motor b = a;
        // b.Maxrpm = b.measureSPEED();
         //b.Power = b.measurePOWER();
         //b.Torque = b.measureTORQUE();
         // compare method needed
         return  ;
        
       }
       else if(customKey == '2'){
        
       }
       else if (customKey == '3'){
        getMode();
       }


      
    }
  }

  
}


void choosefromrecorded(){
 /*int l =sizeof(recordedmotors);
  while(1){
 for(int i=0 ; i< arrlength ; i++ ){

  Serial.print(i+1);
  Serial.print(") ");
  Serial.println(recordedmotors[i].Name);
  
 }
  int x = getnum() -1 ;
  if ( x >arrlength){
    Serial.println("please choose a motor listed");
  }
   else 
     return ;
  
}*/
}





void getMotorParameter(){
 


 
}
  void getMode(){
  

//bool Modeflag =false;
Serial.println("PLEASE CHOOSE MODE");
Serial.println(" 1) measure .");
Serial.println(" 2) test and report . ");
//display.println("Hello, world!");
  //display.display(); 

 
 while(1){
    char customKey = customKeypad.getKey();
    if(customKey){
      
     if(customKey == '1'){
        Modeflag = true;
        measure();
        
        Serial.println(".......THANK YOU.......");

digitalWrite(23,HIGH);
delay(500);
digitalWrite(23,LOW);
delay(100);
digitalWrite(23,HIGH);
delay(500);
digitalWrite(23,LOW);
delay(100);
digitalWrite(23,HIGH);
delay(500);
digitalWrite(23,LOW);


        return;
   
  }

     else if(customKey == '2'){
       Modeflag = true;
       testandreport();


          Serial.println();
       Serial.print("The recorded speed :");
          Serial.println();
       Serial.print("The recorded torque :");
          Serial.println();
       Serial.print("The recorded power :");
          Serial.println();
       Serial.print("The recorded efficiency : ");
          Serial.println();
       Serial.print(".......THANK YOU.......");

       // save in SD card
       return;
      }
    }
  }
}
void measure(){
Serial.println("PLEASE CHOOSE WHAT DO YOU WANT TO MEASURE");
Serial.println(" 1) measure SPEED (rpm) .");
Serial.println(" 2) measure POWER (watt) . ");
Serial.println(" 3) measure TORQUE (n.mm) . ");
Serial.println(" 4) measure ALL . ");
Serial.println(" 5) BACK . ");
while(1){ 
 char customKey = customKeypad.getKey();
 if(customKey){

  if(  customKey == '1'){
   measureSPEED();
    return; 
  }
  else if( customKey == '2' ){
 
 measurePOWER();
 return;  
  }
else if(customKey == '3' ){
  
 measureTORQUE();
  return;    
}
else if(customKey == '4' ){
    
  measureSPEED();
  measurePOWER();
  measureTORQUE();

Serial.print("Mechanical power :");
Serial.print(maxtorque*2*avgRpm*3.14/60);
  
  return; 
}
else if(customKey == '5' ){
   
  getMode();
  
}

  }}}
int measureSPEED (){
  
Serial.println("  measuring SPEED (rpm) ......");
analogWrite(45,0);
 while(digitalRead(A0)== LOW){
  myStepper.setSpeed(50);
  myStepper.step (-50);
  
}
myStepper.step (0);

//int pwm = map(40,0,100,0,255);
digitalWrite(43,HIGH);
digitalWrite(41,LOW);
analogWrite(45,255);
  unsigned long long t =millis();
  unsigned long long t2 = millis()+15000; 

while(millis()<t2){
loops = value/18;
loops2 = value2/18;


if(digitalRead(29)!=a  && digitalRead(29)){
value++;
}
if(digitalRead(35)!=a2  && digitalRead(35)){
value2++;
}
a2=digitalRead(29);
a=digitalRead(35);

if(millis() >=  t+1000){
  t = millis();
  rpm = loops*60;
  value=0;
  
   rpm2 = loops2*60;
   value2=0;


b[count ++] = rpm ;
    
   if(count>14){
    for(int i = 0 ; i<13 ;i++){
      avgRpm= avgRpm + b[i];
   }
      avgRpm =avgRpm/14;
      
   }

   
    if(rpm>maxSpeed){
     maxSpeed =rpm ;
     accelerasion = maxSpeed/millis();
     accelerasion = accelerasion *1000*2*3.14/60;}
  
 // Serial.print(rpm2);
  //Serial.print("----------");
 // Serial.println(rpm);
  } 


}
  Serial.print("No load angular velocity : ");
  Serial.print(2*3.14*avgRpm/60);
  Serial.println(  "rad/s");
  
  Serial.print("accelerasion : ");
  Serial.print(accelerasion);
  Serial.println(  "rad/s2");
 // Serial.print("----------");
  Serial.print("No load Speed : ");
  Serial.print(avgRpm);
  Serial.println(  "Rpm");
analogWrite(45,0);

}



float measurePOWER (){
  
Serial.println("  measuring POWER (rpm) ......");
analogWrite(45,0);

 while(digitalRead(A0)== LOW){
  myStepper.setSpeed(50);
  myStepper.step (-50);
  
}
digitalWrite(43,HIGH);
digitalWrite(41,LOW);
analogWrite(45,255);
unsigned long t3 = millis()+5000;

while(millis()< t3){

unsigned int x=0;
float AcsValue=0.0,Samples=0.0,AvgAcs=0.0,current=0.0;
//analogWrite(6,1023s);
  for (int x = 0; x < 150; x++){ 
  AcsValue = analogRead(A12);        
  Samples = Samples + AcsValue;  
  delay (3); 
}
AvgAcs=Samples/150.0;
current = (2.5 - (AvgAcs * (5.0 / 1024.0)) )/0.066;
power = current/1000*9;
//Serial.println(current);
//Serial.println(power);
}
delay(50);
  analogWrite(4,0);
  
Serial.print(" current : ");
Serial.print(current);
Serial.println(" A");

Serial.print("Electirical Power : ");
Serial.print(power);
Serial.println("watt");
  
  return power;

}




int measureTORQUE (){
  
Serial.println("  measuring TORQUE (N.mm) ......");

analogWrite(45,0);
 while(digitalRead(A0)== LOW){
  myStepper.setSpeed(50);
  myStepper.step (-50);
  
}
myStepper.step (0);

int pwm = map(40,0,100,0,255);
digitalWrite(43,HIGH);
digitalWrite(41,LOW);
analogWrite(45,100);

while(digitalRead(A1) == LOW){
  myStepper.setSpeed(50);
  myStepper.step (50);
  
}
 maxtorque =0;
myStepper.step (0);
 unsigned long t = millis();
 t = t+15000;

while(millis()< t){

pwm = map(100,0,100,0,255);
analogWrite(45,255);

torque =(scale.get_units()*0.453592)*10*6250*9.8/1000;
 //Serial.print("Reading: ");
  //Serial.print((scale.get_units()*0.453592)*100*6250*9.8/1000, 1); 
  //Serial.print(" N.mm"); 
  //Serial.println();

if(torque>maxtorque){
     maxtorque =torque ;
     //accelerasion = maxSpeed/millis();
     //accelerasion = accelerasion *1000*2*3.14/60;
     }
  
}
Serial.print(" maximum torque : "); 
Serial.print( maxtorque); 
Serial.println(" N.mm"); 
  //Serial.println();

analogWrite(45,0);
///if you want to return it back///

while(digitalRead(A0) == LOW){
  myStepper.setSpeed(50);
  myStepper.step (-50);
  
}
myStepper.step (0);

return torque;

}

int getnum(){
 int c =0;
 String b ="";
 Serial.println("please enter your choice and press x to confirm");
  while(1){
    char customKey = customKeypad.getKey();
  if(customKey) {
     Serial.println(customKey);
      b = b+customKey;
      Serial.println(b);
       c = b.toInt();
      Serial.println(c);
       if(customKey == 'x'){
         return c;}
      
    }}}

  

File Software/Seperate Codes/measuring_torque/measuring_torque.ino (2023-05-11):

#include <Stepper.h>

#include "HX711.h"

#define calibration_factor -16650.00 //This value is obtained using the SparkFun_HX711_Calibration sketch

#define LOADCELL_DOUT_PIN  35
#define LOADCELL_SCK_PIN  33

HX711 scale;

int torque;
const int stepsPerRevolution = 200;
Stepper myStepper = Stepper(stepsPerRevolution, 46, 48, 50, 52);


void setup() {
pinMode(25 , INPUT) ;
pinMode(27 , INPUT) ;
pinMode(13 , OUTPUT) ;
pinMode(4 , OUTPUT) ;
pinMode(24 , INPUT) ;
digitalWrite (13, LOW) ;
pinMode(41 , OUTPUT) ;
Serial.begin(115200);
 scale.begin(LOADCELL_DOUT_PIN, LOADCELL_SCK_PIN);
  scale.set_scale(calibration_factor);
  scale.tare();

  Serial.println("processing.....");






  
}

void loop() {
 
  if(digitalRead(24))
   testtorque();

} 






int testtorque(){
 analogWrite(6,0);
 while(digitalRead(27)== HIGH){
  myStepper.setSpeed(50);
  myStepper.step (-50);
  
}
myStepper.step (0);

int pwm = map(40,0,100,0,255);
digitalWrite(41,HIGH);
analogWrite(4,100);

while(digitalRead(25) == HIGH){
  myStepper.setSpeed(50);
  myStepper.step (50);
  
}
myStepper.step (0);
 unsigned long t = millis();
 t = t+15000;

while(millis()< t){

pwm = map(100,0,100,0,255);
analogWrite(4,255);

torque =(scale.get_units()*0.453592)*100*6250*9.8/1000;
 Serial.print("Reading: ");
  Serial.print((scale.get_units()*0.453592)*100*6250*9.8/1000, 1); 
  Serial.print(" N.mm"); 
  Serial.println();
  
}
analogWrite(4,0);
///if you want to return it back///

while(digitalRead(27) == HIGH){
  myStepper.setSpeed(50);
  myStepper.step (-50);
  
}
myStepper.step (0);

return torque;
  
}
